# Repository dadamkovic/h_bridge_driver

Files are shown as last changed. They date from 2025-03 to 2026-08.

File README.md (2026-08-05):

The project is an implementation of an H-bridge driving IC DRV8702QRHBRQ1 that allows control of full H-bridge motor driver in different modes.
The ECU includes:
- buttons for manual control of the motor in both direction + braking
- Status LED
- ON/OFF switch
- Interface for banana plugs and probes
- Interface for electrical control

A chassis designed for 3D printing that protects the ECU. It is inteded to be printed from 3 pieces:
- 2x hard plastic shell (PLA, ABS, ...)
- 1x soft shell for protection against bumps (TPA)






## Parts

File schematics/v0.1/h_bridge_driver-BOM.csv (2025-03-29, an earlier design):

Reference | Value | Datasheet | Footprint | Qty | DNP | Source
C1,C2 | 470u | ~ | Capacitor_THT:CP_Radial_D12.5mm_P5.00mm | 2 |  | https://www.mouser.com/ProductDetail/Nichicon/UVR1J471MHD?qs=E%252BXosmEBrAt7oKLbiFOoGA%3D%3D
C3 | 10u | ~ | Capacitor_SMD:CP_Elec_5x5.3 | 1 |  | https://www.mouser.com/ProductDetail/Wurth-Elektronik/865080642006?qs=0KOYDY2FL2%252BZqx7Z86fIjQ%3D%3D
C4,C6 | 0.1u | ~ | Capacitor_SMD:C_0805_2012Metric_Pad1.18x1.45mm_HandSolder | 2 |  | https://www.mouser.com/ProductDetail/KEMET/C0805C104M5RACTU?qs=sGAEpiMZZMuMW9TJLBQkXgM5fJTMTdHoriBHUpESQJQ%3D
C5,C7,C8 | 1u | ~ | Capacitor_SMD:C_0805_2012Metric_Pad1.18x1.45mm_HandSolder | 3 |  | https://www.mouser.com/ProductDetail/Samsung-Electro-Mechanics/CL21F105ZBFNNNE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
C9,C10 | 2.2u | ~ | Capacitor_SMD:C_0805_2012Metric_Pad1.18x1.45mm_HandSolder | 2 |  | https://www.mouser.com/ProductDetail/TAIYO-YUDEN/UMK212ABJ225KG-T?qs=VWNNG7jHlrIJ3RLc0NcoSg%3D%3D
D1 | RED | ~ | LED_SMD:LED_0805_2012Metric_Pad1.15x1.40mm_HandSolder | 1 |  | https://www.mouser.com/ProductDetail/Lite-On/LTST-C171EKT
D2 | GREEN | ~ | LED_SMD:LED_0805_2012Metric_Pad1.15x1.40mm_HandSolder | 1 |  | https://www.mouser.com/ProductDetail/Lite-On/LTST-S220GKT?qs=sGAEpiMZZMvVL5Kk7ZYykXqPXANRkQ32Tpqd9W7kEBs%3D
D4 | US1M | https://www.diodes.com/assets/Datasheets/ds16008.pdf | Diode_SMD:D_SMA | 1 |  | https://www.mouser.com/ProductDetail/Comchip-Technology/US1M-HF?qs=sPbYRqrBIVnnDQODCBjn5Q%3D%3D
D5 | 2BZX84Cxx | https://diotec.com/tl_files/diotec/files/pdf/datasheets/bzx84c2v4.pdf | Package_TO_SOT_SMD:SOT-23 | 1 |  | https://www.mouser.com/ProductDetail/Diotec-Semiconductor/2BZX84C5V6?qs=OlC7AqGiEDk7Bavv0AXsDw%3D%3D
IC1 | DRV8702QRHBRQ1 | http://www.ti.com/lit/gpn/drv8702-q1 | User_HBridgeDriver:QFN50P500X500X90-33N-D | 1 |  | https://www.mouser.com/ProductDetail/Texas-Instruments/DRV8702QRHBRQ1?qs=%2FP2Ij7fVdhHl2UejmZfGTw%3D%3D
J1,J4,J5 | IN1 | ~ | User_BananaTerminal:BananaPlug-Aliexpress | 3
J2,SW2,SW4 | IN2 | ~ | -- mixed values -- | 3
J3 | SUPP | ~ | User_BananaTerminal:BananaPlug-Aliexpress | 1
J6 | GND | ~ | User_BananaTerminal:BananaPlug-Aliexpress | 1
Q1,Q2,Q3,Q4,Q7 | SUD80460E | https://www.vishay.com/docs/76248/sud80460e.pdf | Package_TO_SOT_SMD:TO-252-2 | 5 |  | https://www.mouser.com/ProductDetail/Vishay-Siliconix/SUD80460E-BE3?qs=7MVldsJ5UawVtXZ3%252BvoTZQ%3D%3D
Q5,Q6 | MUN5336DW1 | https://www.onsemi.com/download/data-sheet/pdf/dtc115ep-d.pdf | Package_TO_SOT_SMD:SOT-363_SC-70-6 | 2
Q9 | MMBTA42 | https://www.onsemi.com/pub/Collateral/MMBTA42LT1-D.PDF | Package_TO_SOT_SMD:SOT-23 | 1 |  | https://www.mouser.com/ProductDetail/Diodes-Incorporated/MMBTA42-7-F?qs=zB6%252Byl1wqIEWwZSkOSfeMQ%3D%3D
R1,R3,R4,R6,R7,R8,R9,R13,R15 | R_US | ~ | -- mixed values -- | 9
R2,R5 | 500R | ~ | Resistor_SMD:R_0805_2012Metric_Pad1.20x1.40mm_HandSolder | 2
R10,R11 | 100R | ~ | Resistor_SMD:R_0805_2012Metric_Pad1.20x1.40mm_HandSolder | 2
R12 | 10k | ~ | Resistor_SMD:R_0805_2012Metric_Pad1.20x1.40mm_HandSolder | 1
R14 | 43k | ~ | Resistor_SMD:R_0805_2012Metric_Pad1.20x1.40mm_HandSolder | 1
SW1 | SW_DIP_x01 | ~ | User_SliderSwitch:EG 1248 | 1
TP1,TP2,TP3,TP4,TP5,TP6,TP7,TP8 | TestPoint | ~ | TestPoint:TestPoint_Pad_D1.5mm | 8
TP9,TP10 | TestPoint_2Pole | ~ | Jumper:SolderJumper-2_P1.3mm_Open_RoundedPad1.0x1.5mm | 2
U2 | MCP1792x-5002xDB | https://ww1.microchip.com/downloads/aemDocuments/documents/APID/ProductDocuments/DataSheets/MCP1792-Family-Data-Sheet-DS20006229D.pdf | Package_TO_SOT_SMD:SOT-223-3_TabPin2 | 1 |  | https://www.mouser.com/ProductDetail/Microchip-Technology/MCP1792-5002H-DB?qs=mAH9sUMRCtvwdyrOK2qV2g%3D%3D

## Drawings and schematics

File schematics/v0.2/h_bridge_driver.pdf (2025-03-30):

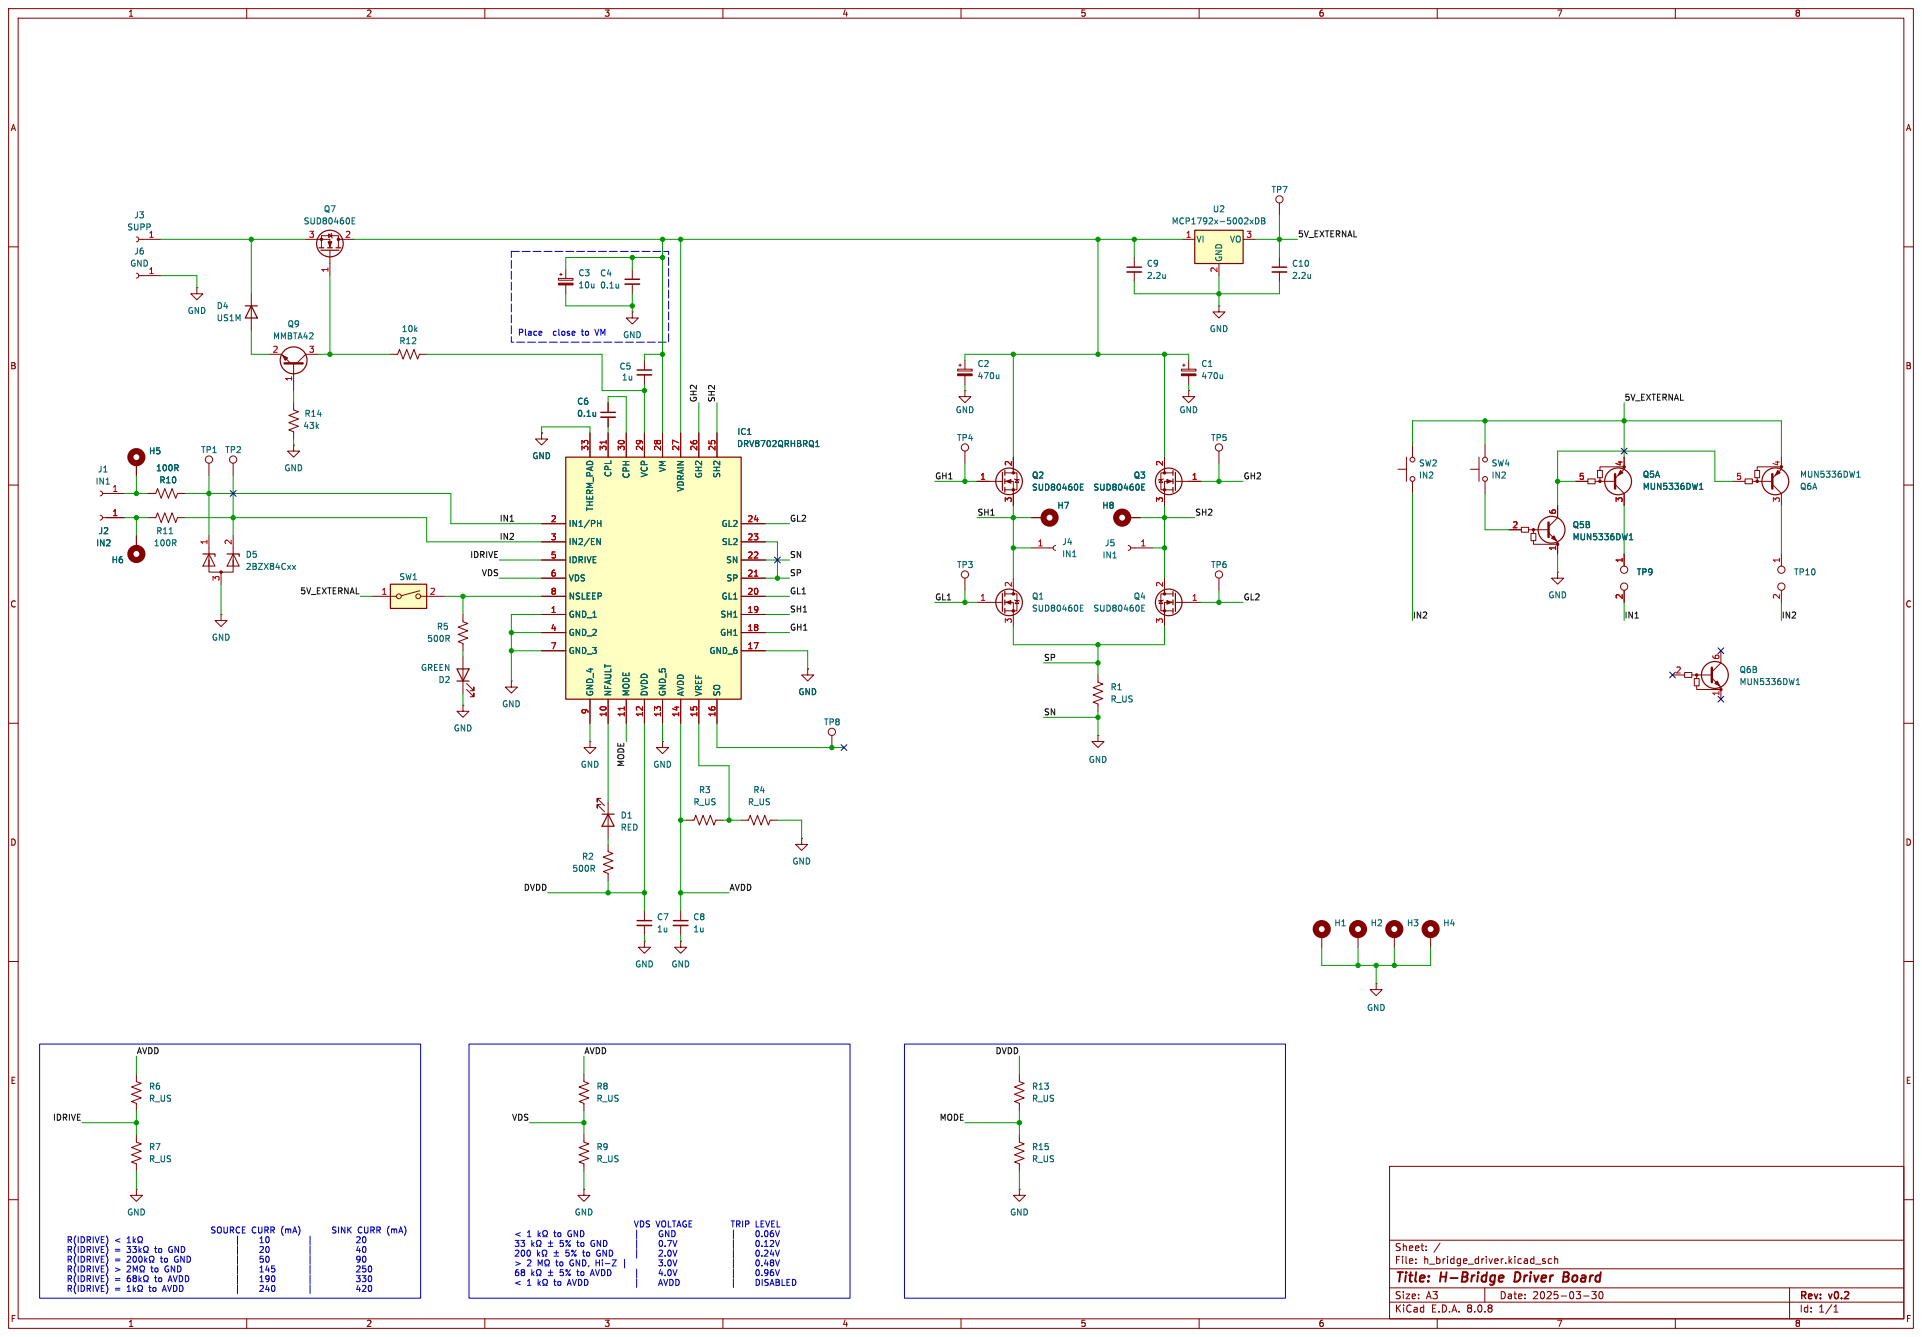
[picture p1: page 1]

R(IDRIVE) < þÿ1k!&| 10 | 20
R(IDRIVE) = þÿ33k!&to GND | 20 | 40
R(IDRIVE) = þÿ200k!&to GND | 50 | 90
R(IDRIVE) > þÿ2M!&to GND | 145 | 250
R(IDRIVE) = þÿ68k!&to AVDD | 190 | 330

33 þÿk©þÿ±5% to GND | 0.7V | 0.12V
200 þÿk©þÿ±5% to GND | 2.0V | 0.24V
68 þÿk©þÿ±5% to AVDD | 4.0V | 0.96V
< 1 þÿk©to AVDD | AVDD | DISABLED

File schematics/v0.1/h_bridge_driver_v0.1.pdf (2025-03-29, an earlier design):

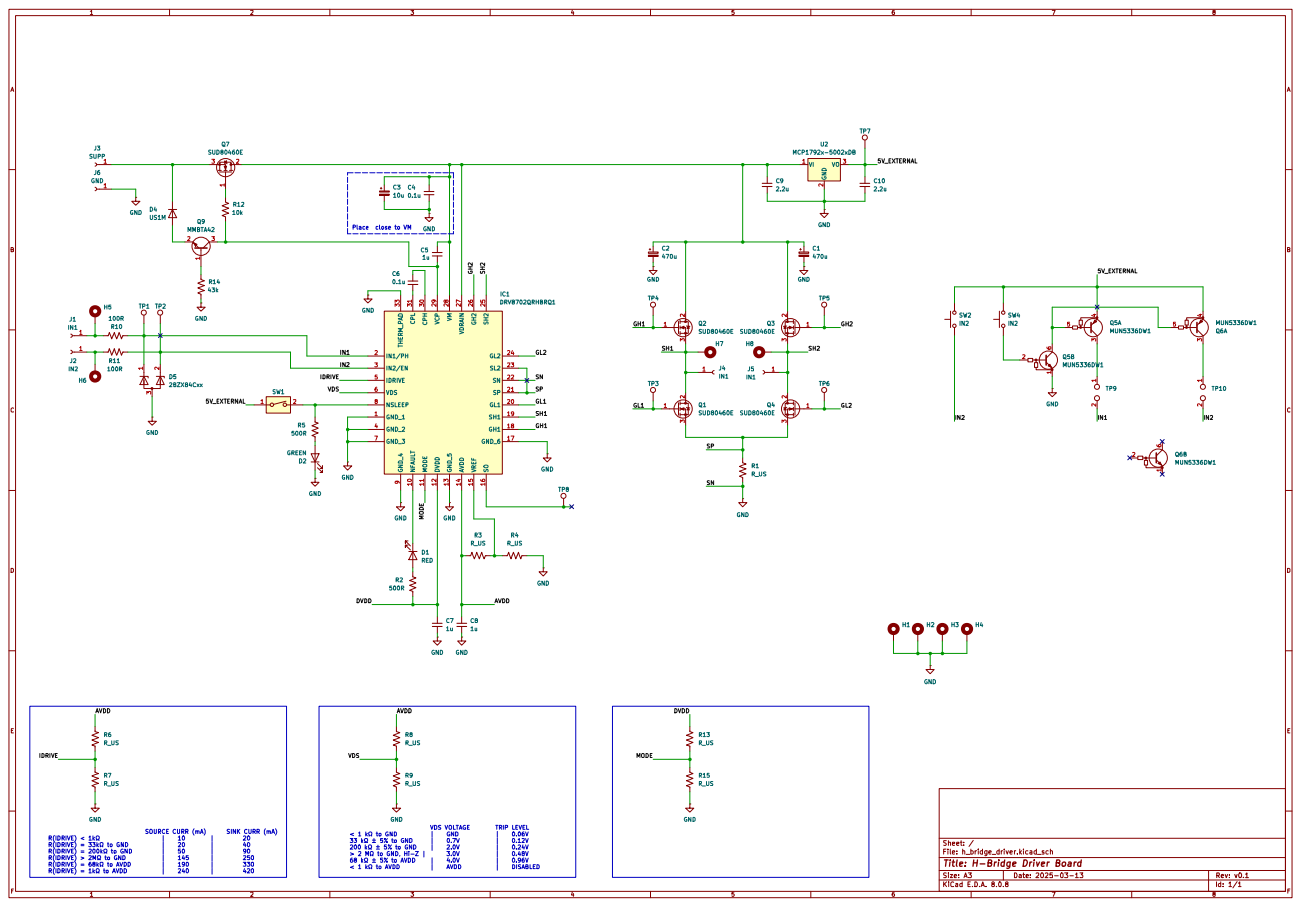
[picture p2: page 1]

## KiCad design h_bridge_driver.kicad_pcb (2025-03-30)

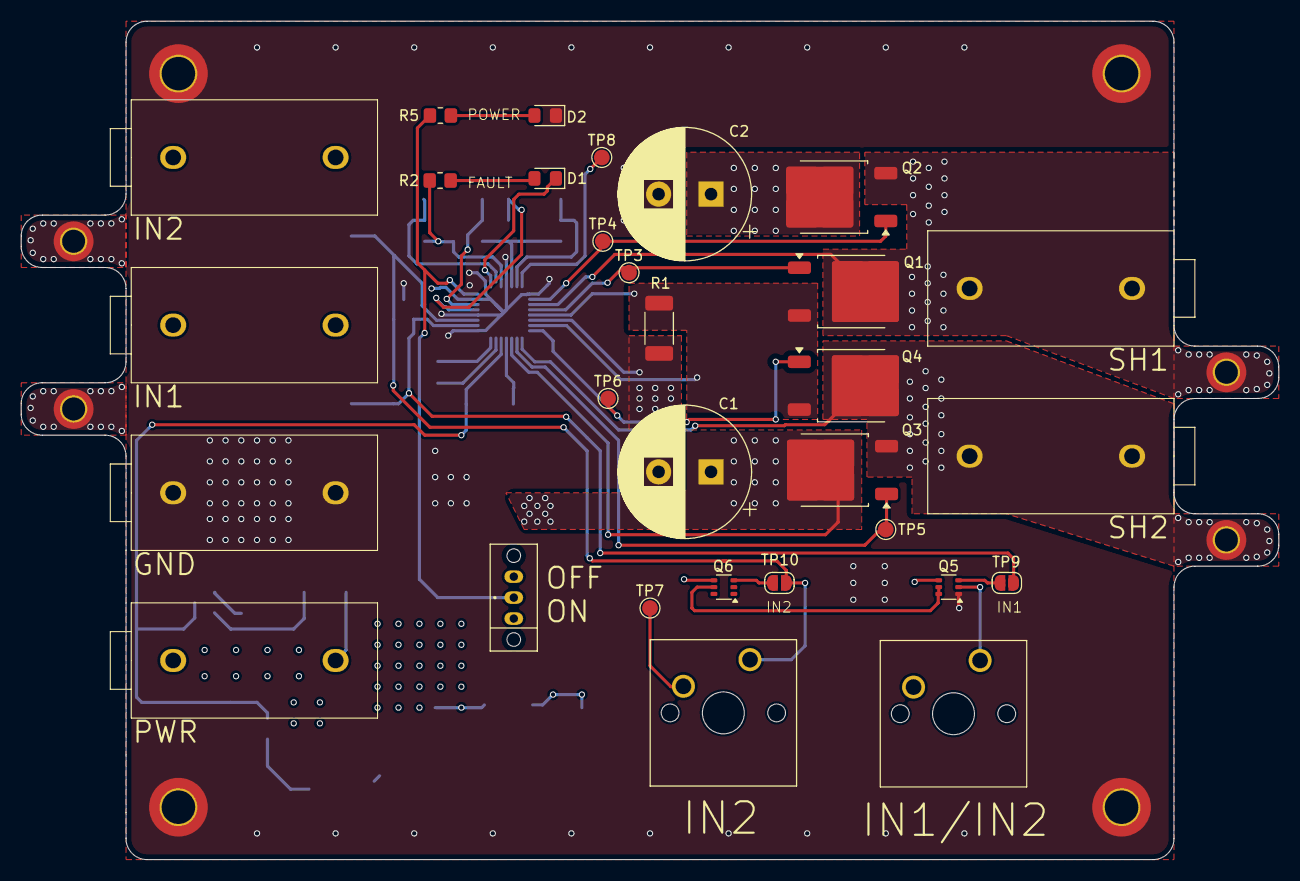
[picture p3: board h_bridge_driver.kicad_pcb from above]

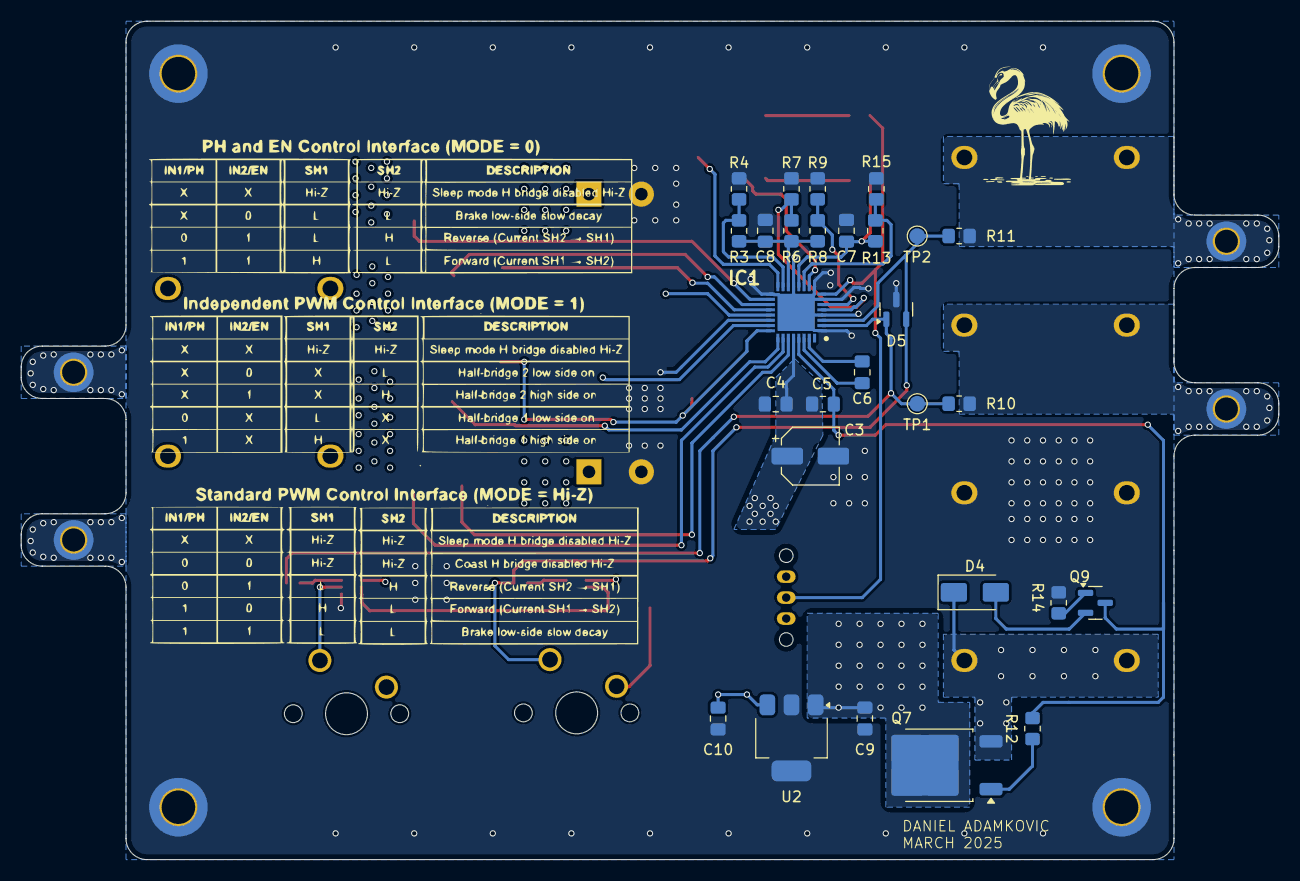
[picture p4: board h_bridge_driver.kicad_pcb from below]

Board: 4 copper layers, 120.0 x 80.0 mm, 66 parts (28 on the bottom side), 35 nets.

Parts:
C1, C2: 470u; CP_Radial_D12.5mm_P5.00mm
C3: 10u; CP_Elec_5x5.3
C4, C6: 0.1u; C_0805_2012Metric_Pad1.18x1.45mm_HandSolder
C5, C7, C8: 1u; C_0805_2012Metric_Pad1.18x1.45mm_HandSolder
C9, C10: 2.2u; C_0805_2012Metric_Pad1.18x1.45mm_HandSolder
D1: RED; LED_0805_2012Metric_Pad1.15x1.40mm_HandSolder
D2: GREEN; LED_0805_2012Metric_Pad1.15x1.40mm_HandSolder
D4: US1M; D_SMA
D5: 2BZX84Cxx; SOT-23
H1, H2, H3, H4: MountingHole_Pad; MountingHole_3.2mm_M3_DIN965_Pad_TopBottom
H5, H6, H7, H8: MountingHole_Pad; MountingHole_2.2mm_M2_DIN965_Pad_TopBottom
IC1: DRV8702QRHBRQ1; QFN50P500X500X90-33N-D
J1, J4, J5: IN1; BananaPlug-Aliexpress
J2: IN2; BananaPlug-Aliexpress
J3: SUPP; BananaPlug-Aliexpress
J6: GND; BananaPlug-Aliexpress
Q1, Q2, Q3, Q4, Q7: SUD80460E; TO-252-2
Q5, Q6: MUN5336DW1; SOT-363_SC-70-6
Q9: MMBTA42; SOT-23
R1: R_US; R_2010_5025Metric_Pad1.40x2.65mm_HandSolder
R2, R5: 500R; R_0805_2012Metric_Pad1.20x1.40mm_HandSolder
R3, R4, R6, R7, R8, R9, R13, R15: R_US; R_0805_2012Metric_Pad1.20x1.40mm_HandSolder
R10, R11: 100R; R_0805_2012Metric_Pad1.20x1.40mm_HandSolder
R12: 10k; R_0805_2012Metric_Pad1.20x1.40mm_HandSolder
R14: 43k; R_0805_2012Metric_Pad1.20x1.40mm_HandSolder
SW1: SW_DIP_x01; EG 1248
SW2, SW4: IN2; SW_Cherry_MX_1.00u_PCB
TP1, TP2, TP3, TP4, TP5, TP6, TP7, TP8: TestPoint; TestPoint_Pad_D1.5mm
TP9, TP10: TestPoint_2Pole; SolderJumper-2_P1.3mm_Open_RoundedPad1.0x1.5mm
U2: MCP1792x-5002xDB; SOT-223-3_TabPin2

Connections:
/5V_EXTERNAL: C10.1, Q5.4 (E1), Q6.4 (E1), SW1.1, SW2.2, SW4.2, TP7.1, U2.3 (VO)
/AVDD: C8.1, IC1.14 (AVDD), R3.1, R6.2, R8.2
/DVDD: C7.1, IC1.12 (DVDD), R2.2, R13.2
/GH1: IC1.18 (GH1), Q2.1 (G), TP4.1
/GH2: IC1.26 (GH2), Q3.1 (G), TP5.1
/GL1: IC1.20 (GL1), Q1.1 (G), TP3.1
/GL2: IC1.24 (GL2), Q4.1 (G), TP6.1
/IDRIVE: IC1.5 (IDRIVE), R6.1, R7.2
/IN1: D5.1 (K), IC1.2 (IN1/PH), R10.2, TP1.1, TP9.2
/IN2: D5.2 (K), IC1.3 (IN2/EN), R11.1, SW2.1, TP2.1, TP10.2
/MODE: IC1.11 (MODE), R13.1, R15.2
/SH1: H7.1, IC1.19 (SH1), J4.1, Q1.2 (D), Q2.3 (S)
/SH2: H8.1, IC1.25 (SH2), J5.1, Q3.3 (S), Q4.2 (D)
/SP: IC1.21 (SP), IC1.23 (SL2), Q1.3 (S), Q4.3 (S), R1.1
/VDS: IC1.6 (VDS), R8.1, R9.2
GND: C1.2, C2.2, C3.2, C4.2, C7.2, C8.2, C9.2, C10.2, D2.1 (K), D5.3 (A), H1.1, H2.1, H3.1, H4.1, IC1.1 (GND_1), IC1.4 (GND_2), IC1.7 (GND_3), IC1.9 (GND_4), IC1.13 (GND_5), IC1.17 (GND_6), IC1.22 (SN), IC1.33 (THERM_PAD), J6.1, Q5.1 (E2), R1.2, R4.2, R7.1, R9.1, R14.1, R15.1, U2.2 (GND)
unnamed: D1.2 (A), R2.1
unnamed: D1.1 (K), IC1.10 (NFAULT)
unnamed: D2.2 (A), R5.2
unnamed: D4.2 (A), Q9.2 (E)
unnamed: D4.1 (K), J3.1, Q7.3 (S)
unnamed: C6.1, IC1.30 (CPH)
unnamed: C6.2, IC1.31 (CPL)
unnamed: IC1.8 (NSLEEP), R5.1, SW1.2
unnamed: C5.2, IC1.29 (VCP), Q9.3 (C), R12.1
unnamed: C1.1, C2.1, C3.1, C4.1, C5.1, C9.1, IC1.27 (VDRAIN), IC1.28 (VM), Q2.2 (D), Q3.2 (D), Q7.2 (D), U2.1 (VI)
unnamed: IC1.15 (VREF), R3.2, R4.1
unnamed: H5.1, J1.1, R10.1
unnamed: H6.1, J2.1, R11.2
unnamed: Q5.5 (B1), Q5.6 (C2), Q6.5 (B1)
unnamed: Q5.3 (C1), TP9.1
unnamed: Q5.2 (B2), SW4.1
unnamed: Q6.3 (C1), TP10.1
unnamed: Q7.1 (G), R12.2
unnamed: Q9.1 (B), R14.2

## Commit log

2025-03-29 First manufactured version of h-bridge-driver
    [h_bridge_driver-BOM.csv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]
2025-03-30 Fixed incorrect plane dimensions on power layer. Fixed wrong connection of BJT to RVP MOSFET gate.
    [h_bridge_driver.kicad_pcb, h_bridge_driver.kicad_sch]
